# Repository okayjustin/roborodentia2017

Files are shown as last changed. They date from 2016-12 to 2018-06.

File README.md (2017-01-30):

# roborodentia2017

To rebuild the newlib libraries (embedded standard C libs):

	cd [REPOSITORY TOP LEVEL DIRECTORY]
	mkdir newlib_arm-none-eabi              					// Or whatever folder name you like
	cd newlib_arm-none-eabi
	../newlib-cygwin/configure
         --target=arm-none-eabi \
         --with-cpu=cortex-m4 \
         --with-fpu=fpv4-sp-d16 \
         --with-float=hard \
         --with-mode=thumb \
         --enable-interwork \        // Not sure if you need this one
         --enable-multilib \         // Not sure if you need this one
         --with-gnu-as \
         --with-gnu-ld \
         --disable-nls \
         --disable-newlib-supplied-syscalls  // Or whatever version of newlib source you have
    sudo make -j4 all

Then take the libc.a and libm.a from newlib_arm-none-eabi/arm-none-eabi/newlib and place them in buildTools.
Also take libnosys.a from newlib_arm-none-eabi/arm-none-eabi/thumb/libgloss/libnosys and place it in buildTools.

Then take the libc.a and libm.a from newlib_arm-none-eabi/arm-none-eabi/fpu/newlib and place them in buildTools.
Also take libnosys.a from newlib_arm-none-eabi/arm-none-eabi/fpu/libgloss/libnosys and place it in buildTools.

Debugging tips:

    > openocd -f firmware/buildTools/st_nucleo_f4.cfg
    > arm-none-eabi-gdb firmware/build/program.elf
    (gdb) target remote localhost:3333
    (gdb) monitor reset halt
    (gdb) b main.c:50
    (gdb) p data[0]
    (gdb) x/1hx 0x40005400

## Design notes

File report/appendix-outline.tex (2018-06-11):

\include{appendices/mechanical_bom}
\include{appendices/schematic}
\include{appendices/layout}
\include{appendices/pcb_bom}
\include{appendices/stm32cubemx_report}
\include{appendices/x_perf}
\include{appendices/y_perf}
\include{appendices/angle_perf}
\include{appendices/all_perf}

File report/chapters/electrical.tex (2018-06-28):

\chapter{Electrical Design}
The electronics of the robot use a combination of off-the-shelf parts and custom designed circuits. An STM32F446RE microcontroller handles low-level hardware control and interfacing such as reading sensors and supplying motor driver control signals while a Raspberry Pi 3 Model B microcomputer processes the data within the artificial neural network and determines motor speeds and directions \cite{stm32f446re}\cite{raspberrypi}. The two processors communicate through a common UART (universal asynchronous receiver-transmitter) link. The other electronic components include a battery, voltage regulation, sensors, motors, and motor drivers.

\section{Power}
A four cell, 1,800 mAH (milliamp-hour) lithium polymer (LiPo) battery powers the entire system. Polarized XT60 connectors provide mechanical reverse polarity protection. The battery voltage varies between 16.8 V when fully charged and 14.8 V when depleted so two off-the-shelf DC-DC switching regulators, shown in Figure \ref{fig:smps}, buck battery voltage down to produce 12 V and 7 V supplies. The high-efficiency switching regulators accept a 7 -- 40 V supply and can output 1.2 -- 35 V at 8 A. The 12 V bus powers the three motor drivers boards while the 7 V bus powers the STM32 Nucleo-64 development board and two AZ1085CD low-dropout linear regulators (LDO) located on the interconnect PCB. One LDO produces a 5 V bus and the other 3.3 V, each at 3 A. The LDOs possess 72 dB power supply rejection ratio, reducing the switching noise. 
\begin{figure}[H]   % [h] means here
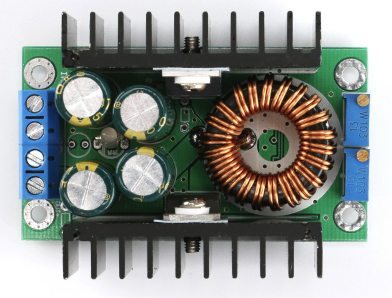
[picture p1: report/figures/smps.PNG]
	\centering 
	\caption{DC-DC Buck Regulator \cite{smps}}\label{fig:smps}
\end{figure}

\section{Sensors}
The robot uses five off-the-shelf sensors for determining its position: four VL53L0X laser rangefinders and one Adafruit 9-DOF inertial measurement unit (IMU).

\subsection{Adafruit 9-DOF IMU}
The Adafruit 9-DOF IMU incorporates the L3DG20H gyroscope and LSM303DLHC accelerometer/compass combo on a single carrier board to allow full inertial measurement in a convenient form factor \cite{adafruit_imu}. Figure \ref{fig:imu} shows the IMU mounted in the 3D printed bracket. The robot uses the accelerometer and magnetic compass to realize a tilt-compensated compass but makes no use of the gyroscope. The LSM303DLHC can measure both acceleration and magnetic fields in three dimensions with configurable bandwidth and full-scale ranges. It uses 400 kHz I\textsuperscript{2}C for control and data transfer and draws power from the 3.3 V supply. 
\begin{figure}[H]   % [h] means here
	\centering 
	\caption{Adafruit 9-DOF IMU Mounted}\label{fig:imu}
\end{figure}
Raw measurements from the IMU possess significant offset and scaling error so a calibration routine is required. The accelerometer and magnetometer calibration process uses the FreeIMU program written by Fabio Varesano \cite{freeimu}. The program features a graphical user interface (GUI), shown in Figure \ref{fig:cal_gui},  to display accelerometer and magnetometer measurements in real time and plots them in 3D space. The calibration program was originally designed to calibrate the open-source FreeIMU IMU when connected to an Arduino with the FreeIMU calibration firmware; the program's device communication back-end was specifically modified for this application to accept the LSM303DLHC IMU connected to an STM32 microcontroller with custom firmware. The calibration algorithm assumes that the sensor's measurements are linearly distorted and therefore produces a linear scaling factor and offset for each of six measurements (accelerometer X, Y, Z and magnetometer X, Y, Z). The correction algorithm is shown in Equation \ref{eq:imu_cal} where $val$ can represent any of the six measurements.
\begin{equation}
\label{eq:imu_cal}
val_{calibrated} = m_{scale} val_{measurement} + b_{offset}
\end{equation}

\begin{figure}[H]   % [h] means here
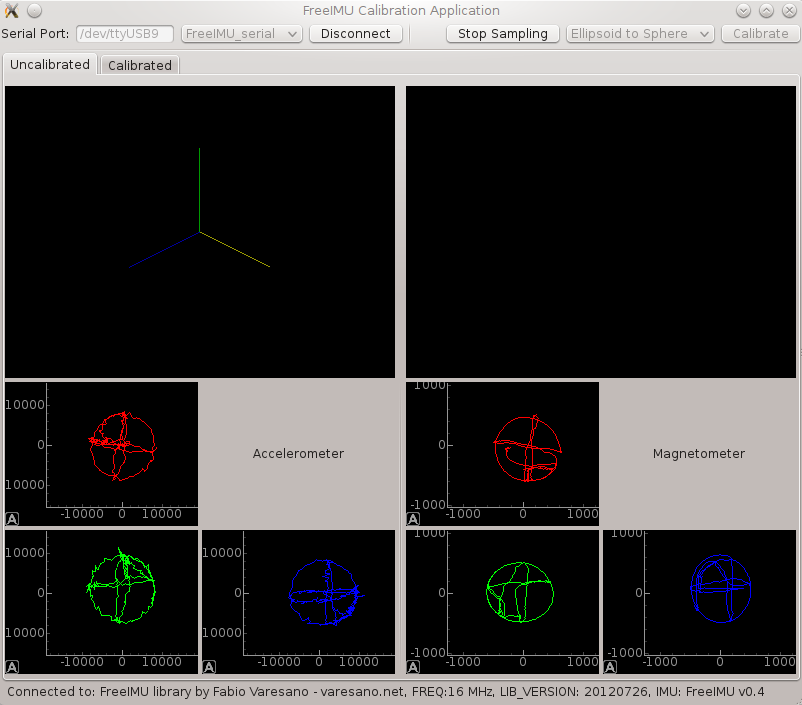
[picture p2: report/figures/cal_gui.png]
	\centering 
	\caption{FreeIMU GUI \cite{freeimu}}\label{fig:cal_gui}
\end{figure}

The calibration procedure is as follows:
\begin{enumerate}
	\item \ssp Mount IMU on fully assembled robot and connect to the microcontroller.
	\item \ssp Connect microcontroller serial port to computer through Serial-to-USB converter.
	\item \ssp Click ``Begin Sampling'' to start recording magnetometer and accelerometer measurements.
	\item \ssp Point the IMU x-axis at the ground and rotate \ang{360} around that axis. Repeat for y-axis and z-axis.
	\item \ssp Point the IMU x-axis at the sky and rotate \ang{360} around that axis. Repeat for y-axis and z-axis.
	\item \ssp Repeat Steps 3 and 4 at least twice to increase data size.
	\item \ssp Click ``Stop Sampling''.
	\item \ssp Click ``Calibrate'' to calculate scaling and offset constants.
\end{enumerate}

Since the IMU is rotated slowly, it experiences a maximum acceleration of 1 G towards the ground as well as a maximum magnetic vector whose specific magnitude and direction depends on the IMU's location on Earth. The procedure ensures that ends of each IMU axis (+X, -X, +Y, -Y, +Z, -Z) eventually receive the maximum acceleration and magnetic field \cite{tedaldi_pretto_menegatti_2014}. To ensure hard-iron errors (such as from motors and permanent magnets) as well as soft iron errors (from local ferromagnetic materials like steel) are compensated for in the calibration, the process should be performed with the fully assembled robot and redone each time the robot is modified \cite{hard_soft_correction}. Since the expected fields are known (acceleration due to gravity, strength of Earth's magnetic field), the required linear transformation can be calculated \cite{freeimu}. Details of the exact algorithm can be found at the FreeIMU website.

\subsection{VL53L0X Rangefinders}
The rangefinders, marketed by STMicroelectronics as the ``world's smallest Time-of-Flight ranging sensor'', are capable of measuring between 30 and 2000 mm with a 30 Hz sample rate \cite{vl53l0x}. They operate by firing pulsed light from a vertical cavity surface emitting laser (VCSEL), measuring time taken for the laser pulse to reflect back, and calculating the distance based on the known speed of light. The robot uses cheap \$8 VL53L0X breakout boards in lieu of designing and assembling custom carriers; the sensor itself comes in a 4.4 x 2.4 mm lead-less package making hand soldering prohibitively difficult. Figure \ref{fig:rangefinder} shows the sensor board mounted in the 3D printed bracket. The sensor breakout boards include the VL53L0X module, decoupling capacitors, an LDO for the sensor's 2.8 V power supply, and level shifters for the I\textsuperscript{2}C lines. Control and data transfer both occur over 400 kHz I\textsuperscript{2}C so the breakout only requires four wires: 3.3 V, ground, and the I\textsuperscript{2}C data and clock lines. To characterize the accuracy and precision of the sensor, distance measurements were taken by targeting the sensor at a sheet of standard white printer paper. The data is compared with measurements from a tape measure; results are shown in Figure \ref{fig:rangefinder_measurement}. 
\begin{figure}[H]   % [h] means here
	\centering 
	\caption{VL53L0X Rangefinder Mounted}\label{fig:rangefinder}
\end{figure}
\begin{figure}[H]   % [h] means here
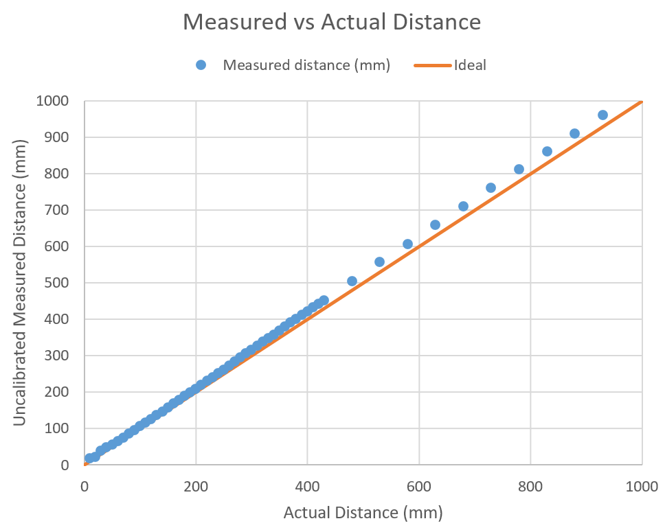
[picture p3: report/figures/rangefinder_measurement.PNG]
	\centering 
	\caption{VL53L0X Measured vs. Actual Distance}\label{fig:rangefinder_measurement}
\end{figure}
Since the measurements primarily appear to possess linear error, only a linear correction is required as in Equation \ref{eq:rf_cal}:
\begin{equation}
\label{eq:rf_cal}
	d_{calibrated} = m_{scale} d_{measurement} + b_{offset}
\end{equation}
$d_{measurement} $ is distance as returned by the sensor, $m_{scale} = 0.96502507$, $b_{offset} = -3.8534743$, and $d_{calibrated}$ is the calibrated distance. The squared error for each data point before and after calibration is shown in Figure \ref{fig:rangefinder_calibrated}. The total squared error for the uncalibrated and calibrated data points are 342.3 mm and 15.0 mm, respectively, indicating the successful use of an appropriate model and constants.
\begin{figure}[H]   % [h] means here
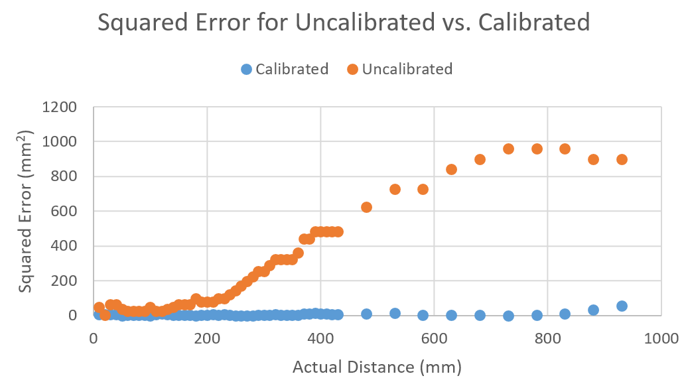
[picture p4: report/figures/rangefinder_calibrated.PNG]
	\centering 
	\caption{VL53L0X Squared Error for Uncalibrated vs. Calibrated}\label{fig:rangefinder_calibrated}
\end{figure}
Additionally, 100 measurements were taken at each distance and the variance computed to characterize the measurement spread. The results are shown in Figure \ref{fig:rangefinder_stddev}. The rangefinders are very accurate; at 900 mm with calibration, the error is only 7 mm or 0.8\% error. Of course, this error is with respect to the average measurement at 900 mm. At 900 mm, the standard deviation is 14 mm so individual measurements can vary, especially with non-ideal surfaces. The closer the target, the more accurate and less varied the measurement. No experiments were carried out to determine the measurement characteristics on various colored, textured, transparent, or angled surfaces as the expected target surface is white painted wood.
\begin{figure}[H]   % [h] means here
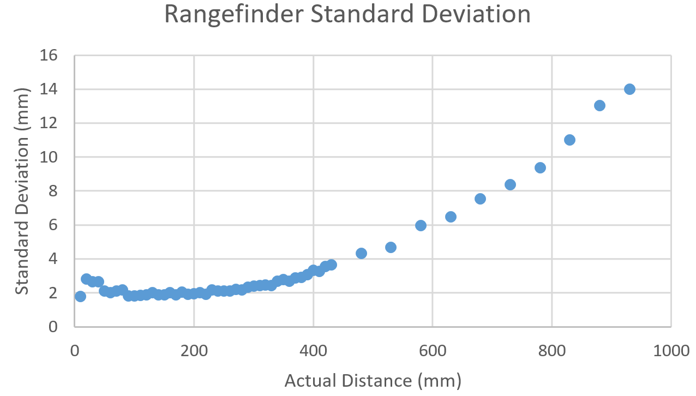
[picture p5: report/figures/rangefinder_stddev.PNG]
	\centering 
	\caption{VL53L0X Standard Deviation}\label{fig:rangefinder_stddev}
\end{figure}
\section{Motors}
The robot uses four 12V Pololu 37D 70:1 geared motors to drive the wheels. The motors draw about 630 mA each at full speed steady state of 234 rpm (24.46 rad/s) and have a maximum acceleration of 4,100 rpm/s (430 rad/s\textsuperscript{2}). These values vary slightly from motor to motor due to slight differences in manufacturing and load. Each wheel experiences slightly different static normal force since the robot's weight is not evenly distributed across the four wheels. Additionally, the dynamic load varies because the ground and base platform are not perfectly flat as well as the minor effects from the robot's weight shifting due to acceleration. The motors come with quadrature rotary encoders which were used in motor characterization but not in the robot itself.

\section{Motor Drivers}
The system uses three off-the-shelf L298N motor driver boards since they are easily obtainable for less than \$6 each and incorporate features such as heat-sinking, flyback voltage protection, supply filtering, and screw terminal connections \cite{l298n_digi}. Implementing comparable motor drivers with a similar feature set would undoubtedly cost more both monetarily and in design effort. The L298N dual H-bridge driver can supply 2\,A maximum output per bridge using a 5 -- 35 V supply. Two motor drivers handle the four robot drive motors while the third powers the blower fan and shooting mechanism motors. 

Figure \ref{fig:l298n} shows a wiring diagram for each motor driver. The board uses four digital control inputs, each controlling the state of one half-bridge. Each motor uses a pair of inputs: IN1 and IN2 control one motor while IN3 and IN4 control the other. To achieve direction and speed control, IN1 and IN3 are pulse width modulated (PWM) while IN2 and IN4 are digitally set. Table \ref{tab:L298N_truth_table} is a truth table of the motor state versus inputs.
\begin{figure}[H]   % [h] means here
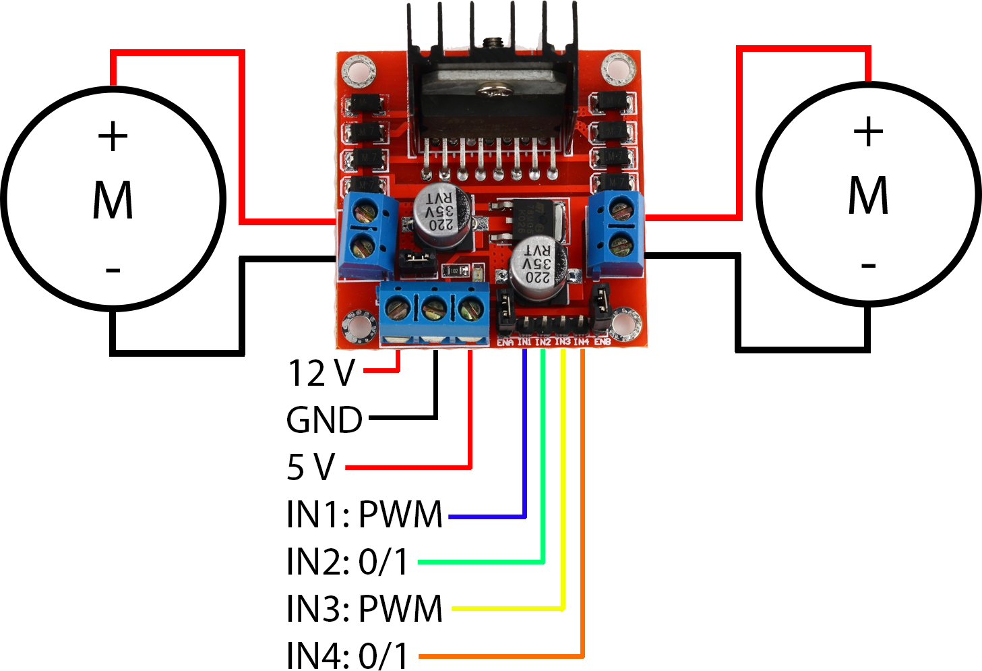
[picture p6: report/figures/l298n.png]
	\centering 
	\caption{L298N Motor Driver Wiring Diagram \cite{l298n}}\label{fig:l298n}
\end{figure}
\begin{table}[h]
	\centering \caption{Motor Control Truth Table}	\label{tab:L298N_truth_table}
	\begin{tabular}{ccc}
		\toprule 
		IN1/IN3 Duty Cycle & IN2/IN4 State & Motor State \\ 
		\midrule 
		0\% & 0 & Stopped \\ 
		\textgreater 0\% & 0 & Forward, speed increases with duty cycle \\ 
		\textless 100\% & 1 & Reverse, speed decreases with duty cycle \\ 
		100\% & 1 & Stopped \\ 
		\bottomrule
	\end{tabular} 
\end{table}

\section{Servo}
A GWS S03N standard servo powered from the 5 V bus actuates the gating mechanism in the ball hopper. Most servos are controlled by driving the control wire with a pulse width modulated (PWM) signal with a period of 15 -- 25 ms and a pulse width between 0.5 ms and 2.5 ms where the pulse width determines the position of the servo as shown in Figure \ref{fig:servo_pulse_width}. 
\begin{figure}[H]   % [h] means here
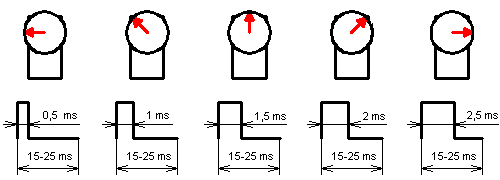
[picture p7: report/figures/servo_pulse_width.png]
	\centering 
	\caption{Servo PWM Control Scheme \cite{servo_pulse_width}}\label{fig:servo_pulse_width}
\end{figure}
Due to loose tolerances, the actual required pulse widths can vary from servo to servo, requiring calibration to obtain accurate positional control. The process for calibration is simple: apply various pulse widths and record the resulting servo positions. The calibrated pulse widths and servo angles are recorded in Table \ref{tab:servo_angles}. Clearly, the actual required timings for specific angles possess significant deviations from nominal. 
\begin{table}[h]
	\centering \caption{Servo Required Pulse Widths}	\label{tab:servo_angles}
	\begin{tabular}{cc}
		\toprule 
		Servo Position & Pulse Width (ms) \\ 
		\midrule 
		\ang{0} & 0.674 \\ 
		\ang{45} & 1.082 \\
		\ang{90} & 1.490 \\ 
		\ang{135} & 1.898 \\ 
		\ang{180} & 2.306 \\ 
		\bottomrule 
	\end{tabular} 
\end{table}

\section{Microcontroller}
An STMicroelectronics STM32F446RE microcontroller (MCU) serves as the bridge between the robot's low-level electronics and the high-level control system running on a desktop computer. Specifically, the MCU collects data from sensors over I\textsuperscript{2}C and general purpose input/output (GPIO), generates control signals for the motor drivers and servo, and services commands from UART. The MCU resides on an STMicroelectronics Nucleo-64 development board, shown in Figure \ref{fig:nucleo64}, which conveniently integrates an ST-LINK V2 debugger, programmer, and USB-to-UART interface. The MCU uses an ARM Cortex-M4 RISC (reduced instruction set computer) core running at 180 MHz with hardware FPU (floating point unit) and adaptive real-time accelerator. It provides numerous communication interfaces, timers, and GPIO as well as DMA (direct memory access) capability. The development board itself plugs into a board-to-board receptacle located at the bottom of the interconnect PCB.
\begin{figure}[H]   % [h] means here
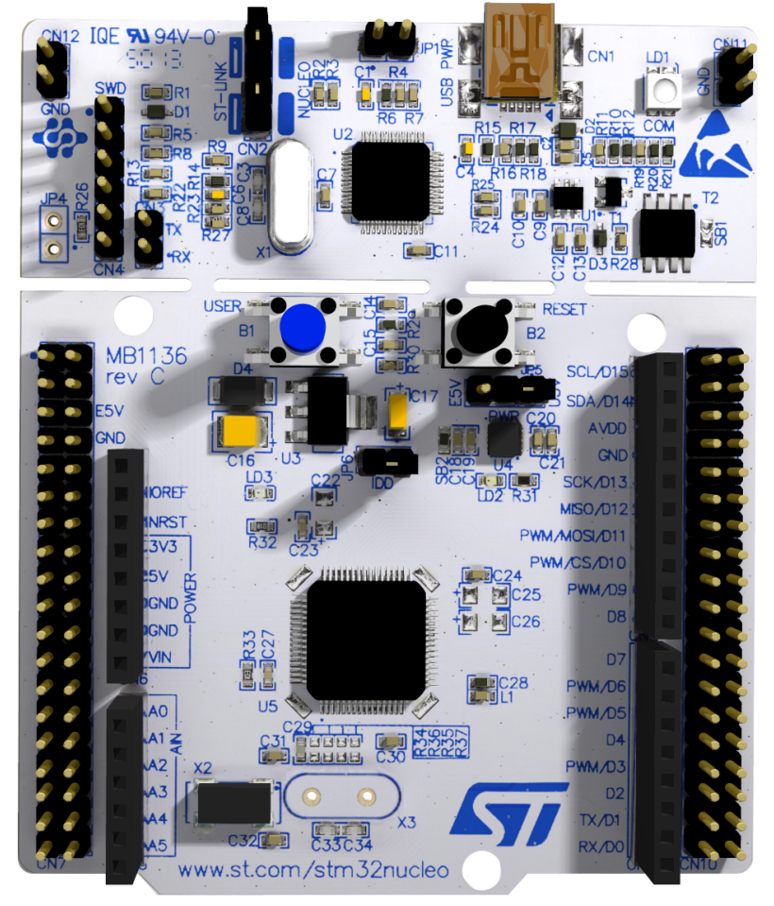
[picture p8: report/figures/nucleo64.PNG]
	\centering 
	\caption{STM32 Nucleo-64 Development Board \cite{nucleo64_manual}}\label{fig:nucleo64}
\end{figure}

\section{Interconnect PCB}
The interconnect PCB is a custom designed board with three goals: regulate voltage, route power, and connect peripherals to the development board. The PCB routes input battery power to two external buck regulators, producing 12 V and 7 V. The 7 V bus is further regulated to 5 V and 3.3 V logic rails using two AZ1085CD LDOs and then routed to the development board, sensors, etc. Most importantly, the interconnect board provides dedicated 2.0 mm JST connectors for all sensors, motor drivers, and the servo to simplify and robustify wiring across the robot. In addition, hand-crimped cables made with JST connectors and 28 gauge ribbon cable prevent disorganized point-to-point wiring. A block diagram is shown in Figure \ref{fig:interconnect_block}. The board incorporates support for additional sensors to address uncertainty in the robot's final design. Table \ref{tab:interconnect_features} lists the supported features as well as those used in the final design. 
\begin{figure}[H]   % [h] means here
	\centering 
	\caption{Electronics Block Diagram}\label{fig:interconnect_block}
\end{figure}
\begin{table}[h]
	\centering	\caption{Interconnect PCB -- Supported Features}	\label{tab:interconnect_features}
	\begin{tabular}{ccl}
		\toprule 
		Qty Available & Qty Used & \multicolumn{1}{c}{Feature} \\ 
		\midrule 
		6 & 4 & VL53L0X laser rangefinder \\ 
		1 & 1 & Adafruit 9-DOF IMU \\ 
		3 & 3 & Dual H-bridge motor driver \\
		2 & 1 & 5 V Standard servo \\ 
		2 & 0 & Infrared proximity array \\
		4 & 0 & Microswitch \\ 
		4 & 2 & Debug LED \\ 
		1 & 1 & Debug button \\
		1 & 1 & Reset button \\ 
		\bottomrule
	\end{tabular} 
\end{table}
Due to limited MCU GPIO availability, the board incorporates three TCA9554ADWR I\textsuperscript{2}C 8-bit GPIO expanders to handle low-speed signals \cite{TCA9554ADWR}. However, either through an indeterminate design error, defective ICs, or poor soldering, none of the ICs would respond to I\textsuperscript{2}C traffic so they were not used in the final design. The GPIOs meant for the microswitches were repurposed to drive some signals instead.

The system uses two 400 kHz I\textsuperscript{2}C buses to improve communication bandwidth with the numerous I\textsuperscript{2}C devices. Table \ref{tab:i2c_table} lists I\textsuperscript{2}C device addresses and bus allocation. The two buses are named I2C2 and I2C3 to maintain parity with the microcontroller's naming convention.
\begin{table}[h]
	\centering	\caption{Interconnect PCB -- I\textsuperscript{2}C Devices}  \label{tab:i2c_table}
	\begin{tabular}{clc}
		\toprule 
		\multicolumn{1}{c}{I\textsuperscript{2}C Bus} & \multicolumn{1}{c}{Device} & Address (7-bit) \\ 
		\midrule 
		I2C2 & Rangefinder 4 & 0x52 \\  
		I2C2 & Rangefinder 5 & 0x53 \\  
		I2C2 & Rangefinder 6 & 0x54 \\  
		I2C2 & Adafruit 9-DOF IMU Gyroscope & 0x69 \\ 
		I2C2 & Adafruit 9-DOF IMU Accelerometer & 0x19\\ 		
		I2C2 & Adafruit 9-DOF IMU Magnetometer & 0x1E \\ 		
		I2C2 & GPIO Expander 3 & 0x3A \\ 				
		\hline
		I2C3 & Rangefinder 4 & 0x52 \\  
		I2C3 & Rangefinder 5 & 0x53 \\  
		I2C3 & Rangefinder 6 & 0x54 \\  
		I2C3 & GPIO Expander 1 & 0x38 \\ 				
		I2C3 & GPIO Expander 2 & 0x39 \\ 
		\bottomrule				
	\end{tabular} 
\end{table}
The schematic capture and board layout were created in CadSoft EAGLE 7.4 due to its simplicity of use, popularity, and community support \cite{eagle}. The schematic can be found in Appendix \ref{appendix:schematic}, layout in Appendix \ref{appendix:layout}, and bill of materials in Appendix  \ref{appendix:pcb_bom}. The board uses two 1-ounce copper layers for cost effectiveness. Two large headers underneath the board connect to the headers on the top of the microcontroller development board while the JST connectors are placed across the top of the PCB. 18-gauge wires soldered to large plated through-holes at the right edge of the board connect the external buck regulators. All components are placed on the top side of the board (except for the development board connectors) to make hand-soldering easier. The bare PCBs, fabricated by PCBWay.com, cost \$23 for 10 copies \cite{pcbway}. The completed electronics assembly is shown in Figure \ref{fig:full_electronics}.
\begin{figure}[h]   % [h] means here
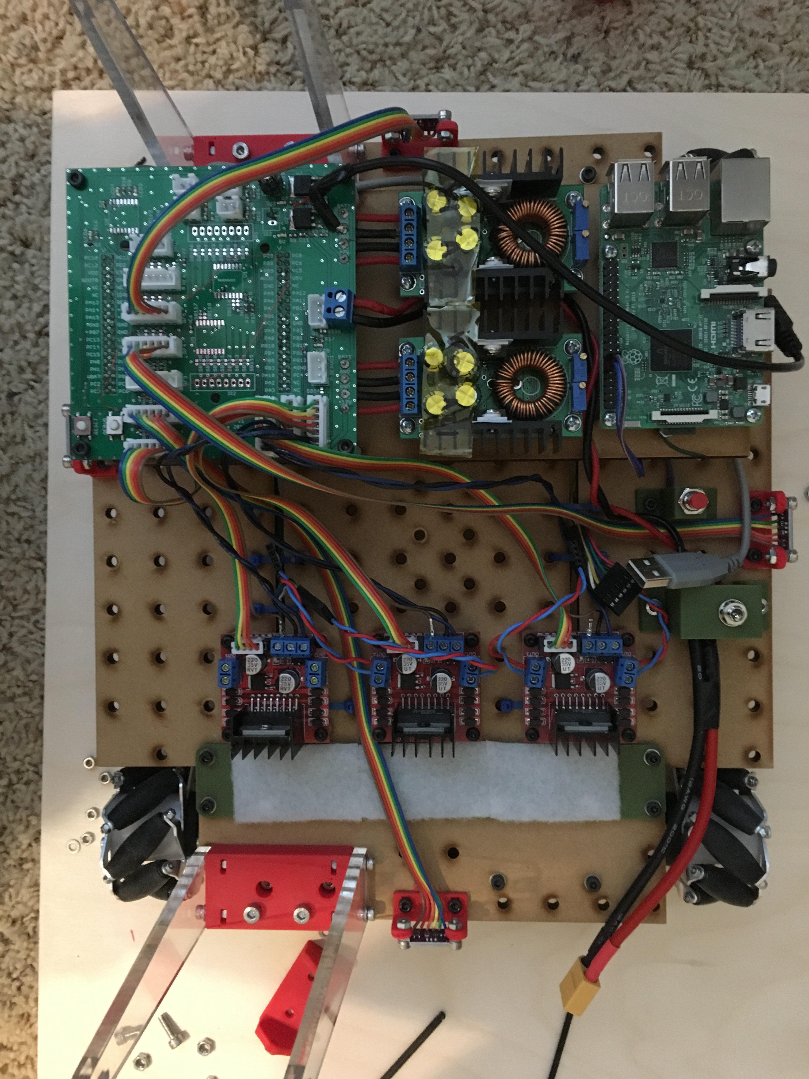
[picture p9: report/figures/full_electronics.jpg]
	\centering 
	\caption{Fully Assembled Electronics}\label{fig:full_electronics}
\end{figure}

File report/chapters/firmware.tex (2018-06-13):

\chapter{Firmware Design}
\section{STM32CubeMX}
The robot uses an STMicroelectronics STM32F446RE microcontroller (MCU) for low level sensor interfacing and motor control signal generation. The MCU sends filtered sensor data to a Raspberry Pi \cite{raspberrypi} and receives speed and direction commands for each motor. Before starting the electrical design, the various hardware signals must be assigned to the MCU's GPIO with consideration for the device's peripherals such as timers and I\textsuperscript{2}C buses, a process aided by STMicroelectronics' configuration program, STM32CubeMX, shown in Figure \ref{fig:stm32cubemx} \cite{stm32cubemx}. Within the program, the user selects which MCU to configure and a graphical representation of the chip is shown in the GUI. The MCU's GPIO pins are arranged into banks of up to 16 pins each called ports. For example, PC2 is the second pin in Port C while PB11 is Pin 11 in Port B. The left column of the GUI lists the device peripherals including analog-to-digital converters (ADCs); various buses such as SPI, USART, and USB; and timers. Peripheral settings can be chosen here such as USART mode (asynchronous, single-wire, LIN, etc) and flow control as well as timer clock sourcing and channel modes.
\begin{figure}[H]   % [h] means here
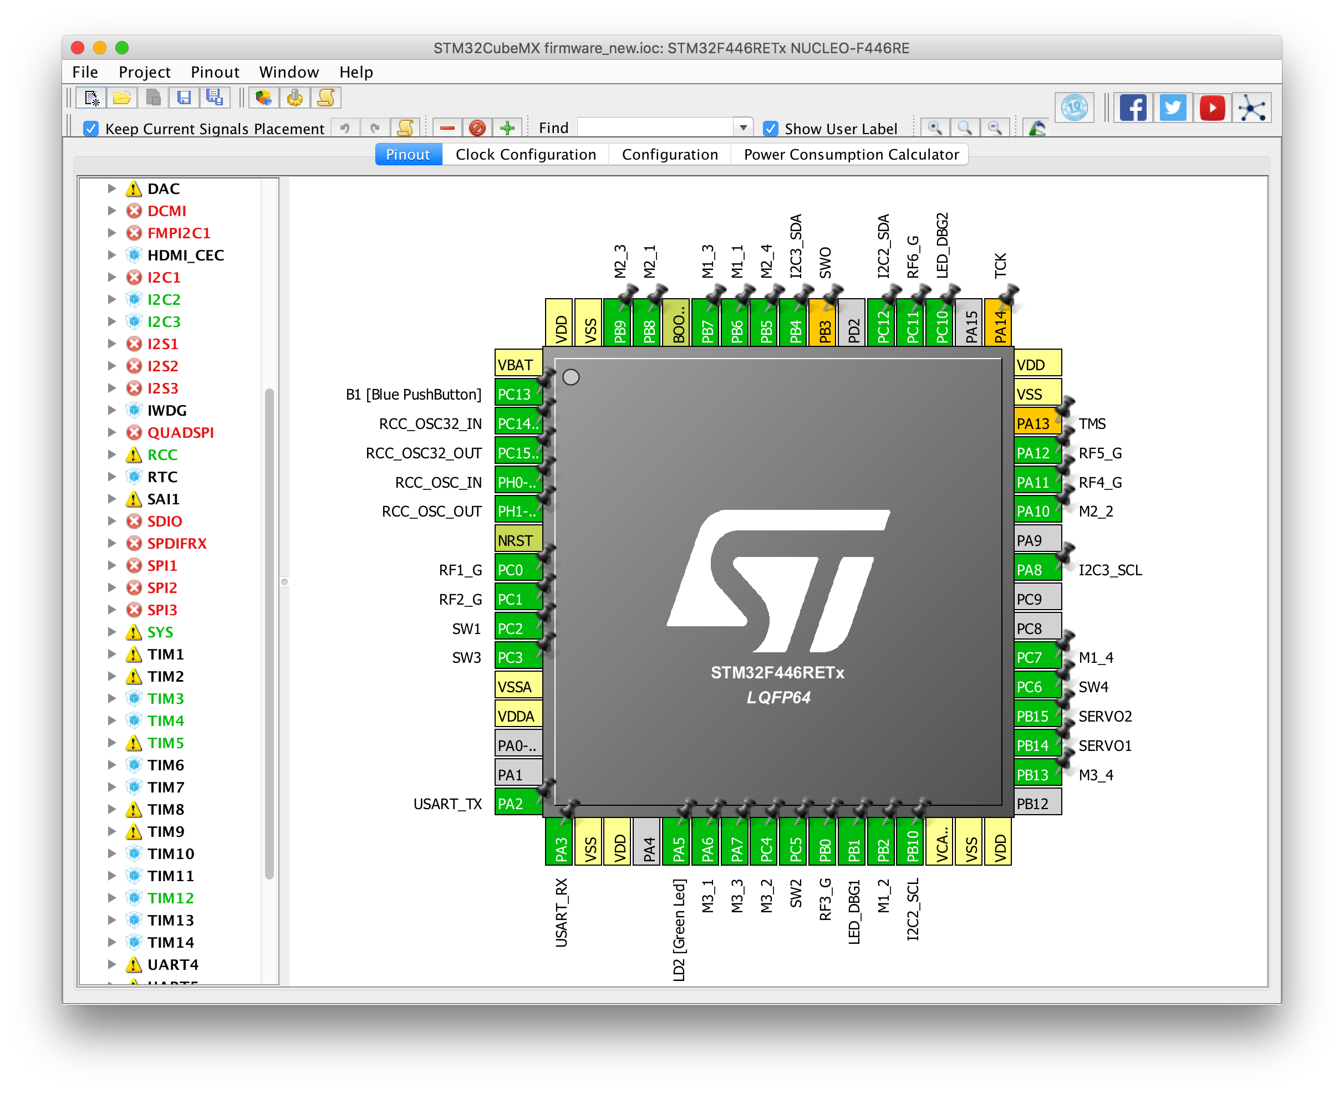
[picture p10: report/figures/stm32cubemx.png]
	\centering 
	\caption{STM32CubeMX}\label{fig:stm32cubemx}
\end{figure}
The program greatly reduces development effort. Clicking a pin on the GUI brings up a menu of possible assignments. For example, clicking PB15, seen in Figure \ref{fig:stm32cubemx_pin}, shows that the pin can be used for the ADC, I2S2, as SPI2's MOSI, TIMER12's CH2 output, part of the USB differential data pair, as standard GPIO input or output, and more. As pins are assigned to various purposes, the program continually checks for compatibility issues and pin conflicts so a user can iteratively assign pins until all errors clear. For example, using a particular set of timers may actually prevent the use of I2C1 so either I2C2 or I2C3 must be used instead. This process is much faster and less error-prone than searching through the MCU's immense datasheet to manually check for assignment conflicts within every peripheral.
\begin{figure}[H]   % [h] means here
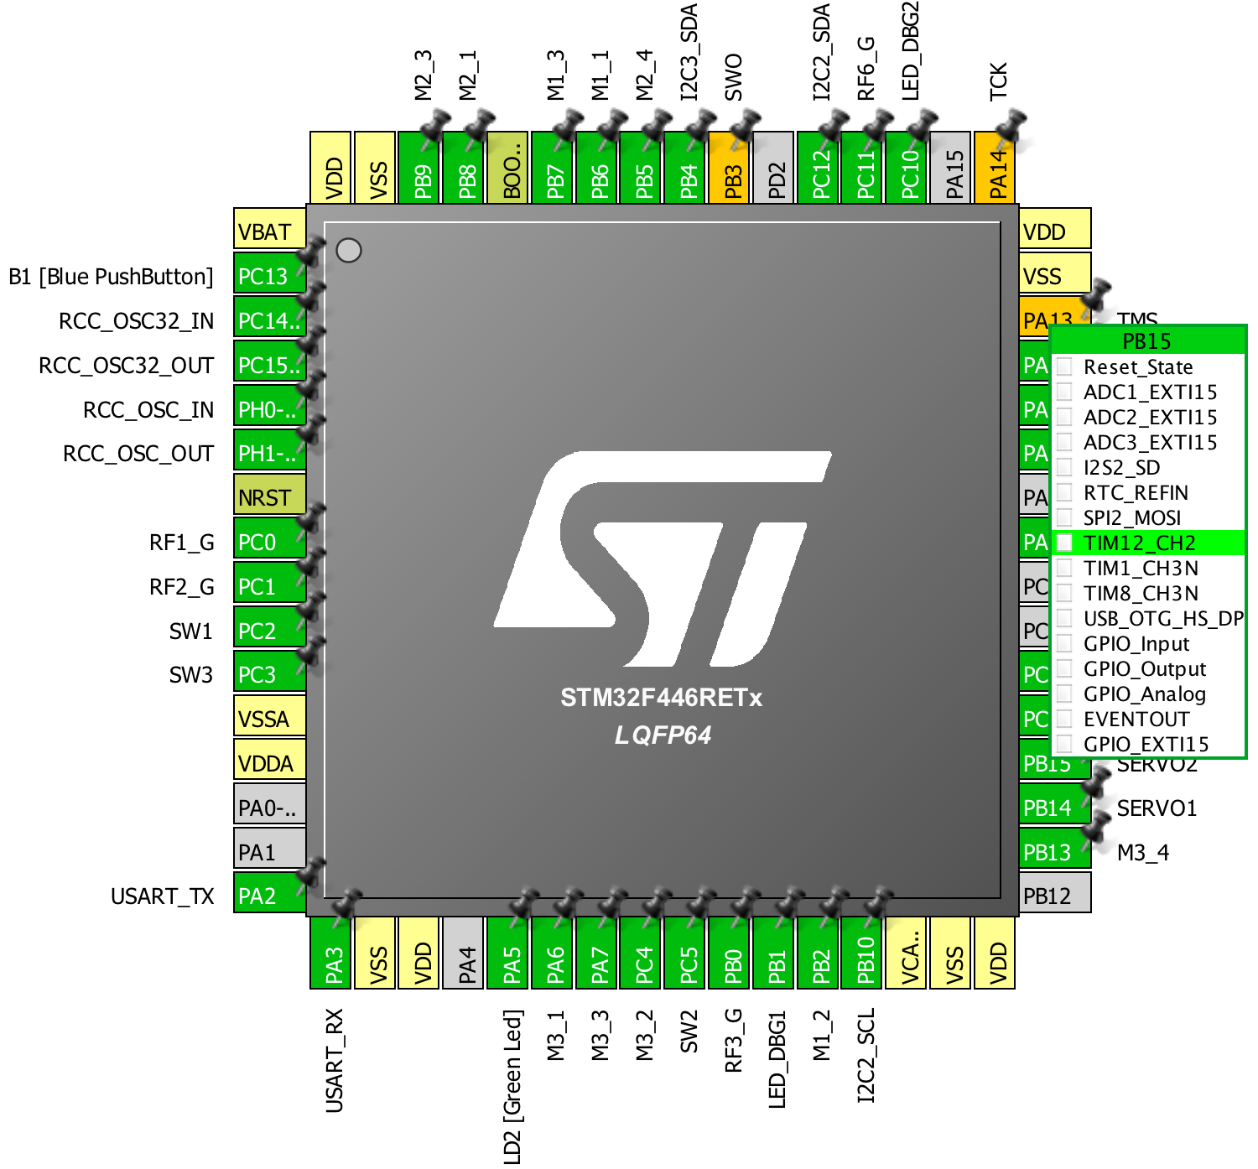
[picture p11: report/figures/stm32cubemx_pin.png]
	\centering 
	\caption{STM32CubeMX -- Pin Menu}\label{fig:stm32cubemx_pin}
\end{figure}
The software also provides device-wide clock and PLL configuration as shown in Figure \ref{fig:stm32cubemx_clocks}. The MCU uses an external 8 MHz crystal to drive the internal PLL which then generates a 180 MHz system clock. Since the system is optimized for performance instead of power-saving, the advanced peripheral bus (APB) clocks run at 45 MHz and 90 MHz for APB1 and APB2, respectively \cite{stm32f446re}. 
\begin{figure}[H]   % [h] means here
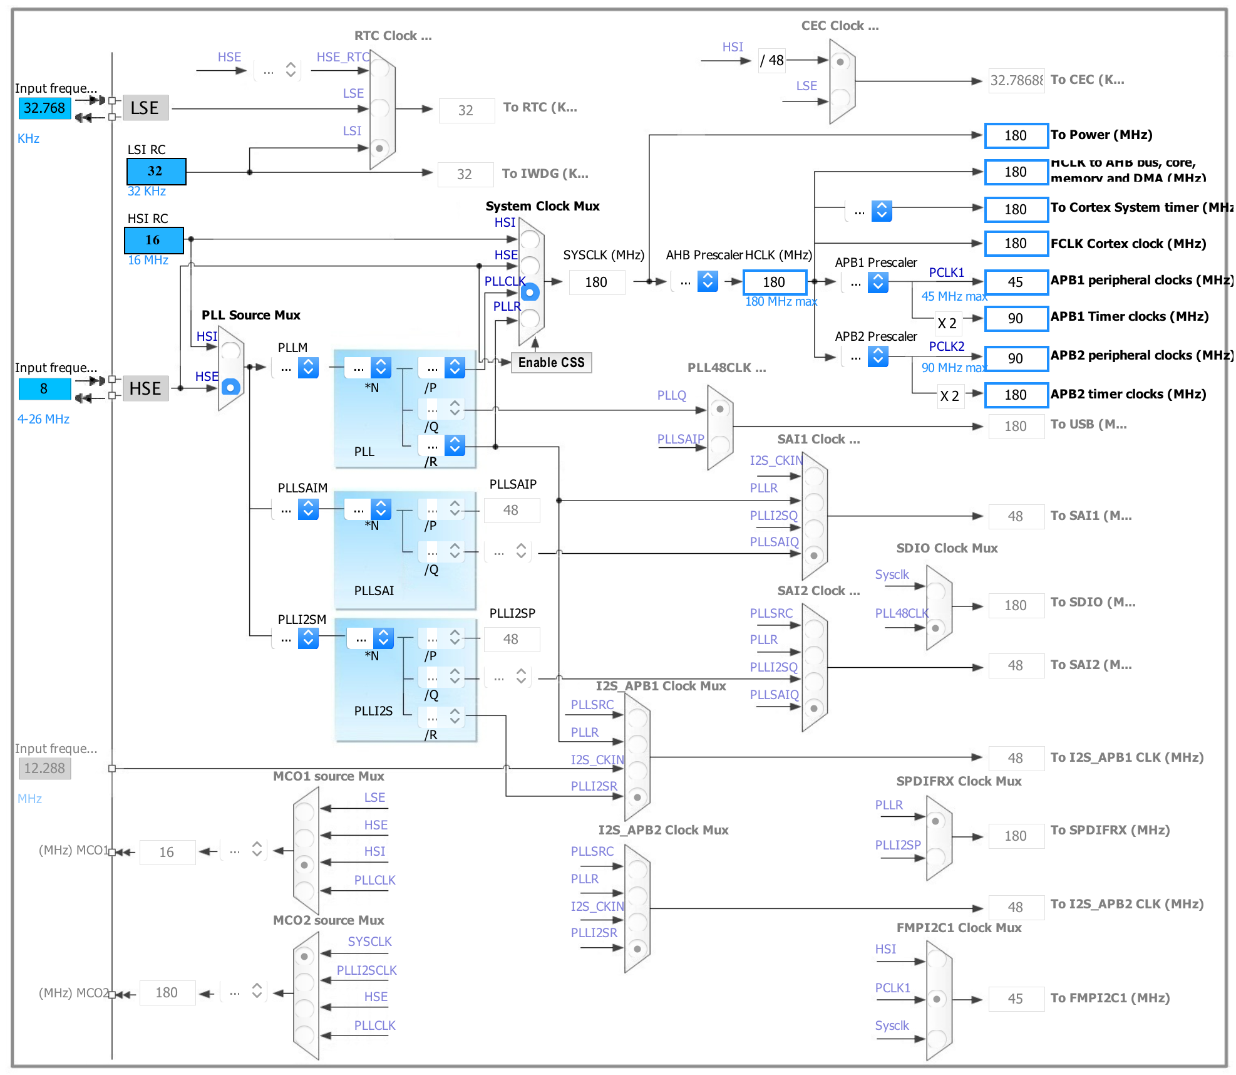
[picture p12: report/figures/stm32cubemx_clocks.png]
	\centering 
	\caption{STM32CubeMX -- Clock Configurator}\label{fig:stm32cubemx_clocks}
\end{figure}
Another tab within STM32CubeMX provides detailed peripheral configuration, shown in Figure \ref{fig:stm32cubemx_config}. Both I\textsuperscript{2}C buses are set to 400 kHz with a 2:1 T\textsubscript{low}:T\textsubscript{high} duty cycle to meet the minimum pulse width requirement of slave devices. The USART peripheral is configured to 921,600 bits/s, 8-bit words, no parity, and one stop bit. The direct memory access (DMA) controller is set to process requests from the I\textsuperscript{2}C and UART peripherals to reduce processor load. 
\begin{figure}[H]   % [h] means here
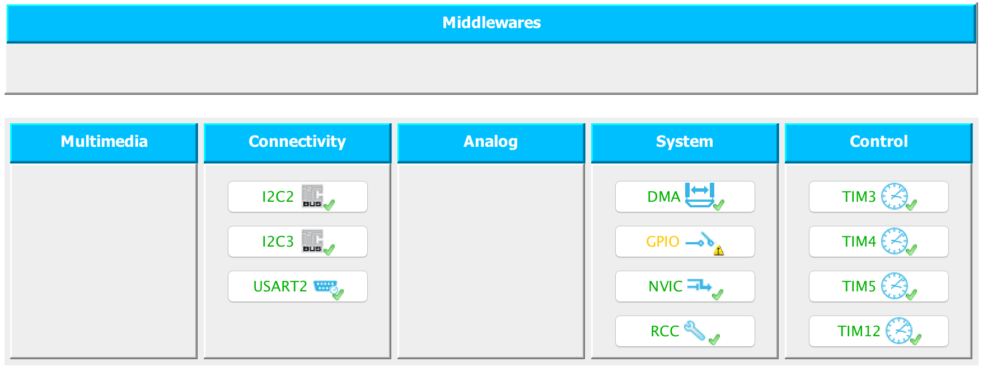
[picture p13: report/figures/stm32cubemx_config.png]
	\centering 
	\caption{STM32CubeMX -- Peripheral Configurator}\label{fig:stm32cubemx_config}
\end{figure}
The robot uses four of the MCU's timers: TIMER3, TIMER4, TIMER5, and TIMER12. Each of these timers sources its base clock from the APB1 clock which is 90 MHz. TIMER3 and TIMER4 output 6 PWM control signals for the motor drivers. They are set to count upward and reset after the counter reaches 2047 to produce a 43.9 kHz PWM frequency in the ultrasonic range. TIMER5, used for delay and timing functions, employs a clock prescaler of 9000 so the counter increases every 0.1 ms and never resets; the 32-bit counter has a maximum value of 4,294,967,295 corresponding to a counter rollover period of about 5 days. Finally, TIMER12 drives the PWM signals for servo control. It uses a 45 prescaler and a 50,000 counter period to produce a 40 Hz PWM frequency.

After configuring the various items above, STM32CubeMX can generate common boilerplate plate code to initialize and configure all the devices. Include and source files are generated on a by-peripheral basis to compartmentalize code. The program also generates a report of the device configuration, attached in Appendix \ref{appendix:stm32cubemx_report}.

\section{Microcontroller Firmware}
The firmware, written in C and compiled with gcc, consists of a main file in conjunction with peripheral driver files \cite{gcc}. The dependency graph is shown in Figure \ref{fig:firmware_dependencies} with file descriptions shown in Table \ref{tab:firmware_file_desc}.  STM32CubeMX automatically generated several files to which user code was added for specific robot functions. The VL53L0X API, provided by STMicroelectronics, was also modified for the STM32F446 platform. Table \ref{tab:firmware_specs} lists the firmware requirements.
\begin{figure}[H]   % [h] means here
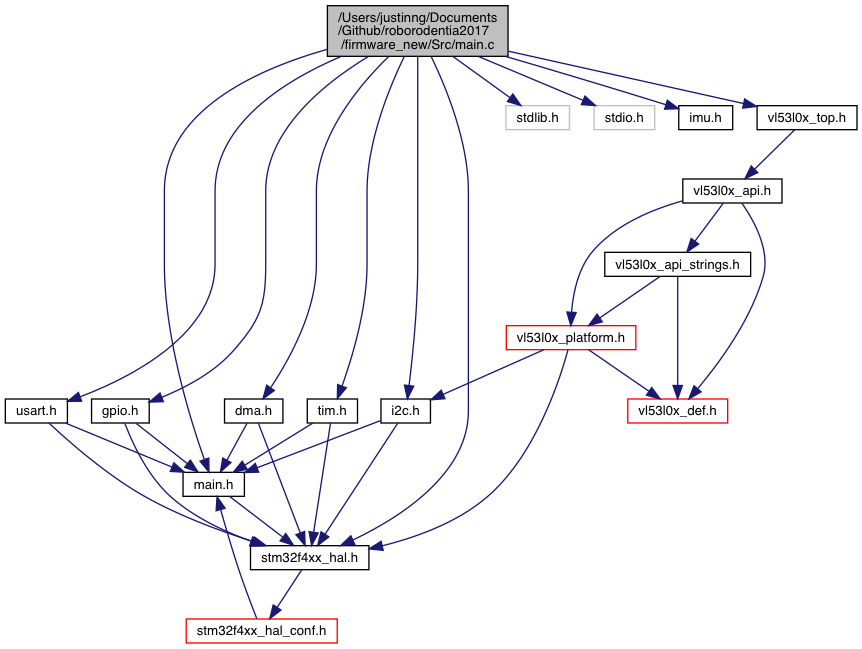
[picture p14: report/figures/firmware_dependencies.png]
	\centering 
	\caption{Firmware Dependency Graph for main.c}\label{fig:firmware_dependencies}
\end{figure}
\begin{table}[H]
	\centering	\caption{Firmware -- Source File Summary} 	\label{tab:firmware_file_desc}
	\begin{tabular}{r|l}
		\toprule 
		\multicolumn{1}{c}{File (.h/.c)} & \multicolumn{1}{c}{Description} \\ 
		\midrule 
		main & Initialization and main loop. \\  
		stm32f4xx\_hal & Hardware abstraction layer driver. \\  			
		dma & Sets up DMA priorities and enables DMA interrupts. \\  		
		i2c & Initializes I\textsuperscript{2}C buses, read/write, finds active devices. \\  		
		tim & Initializes timers 3, 4, 5, and 12. \\  		
		usart & Initializes UART, functions to write to bus, DMA callbacks. \\  		
		gpio & Configures GPIO modes (in/out), speeds, and pull-ups/pull-downs. \\  		
		vl53l0x\_top & STMicroelectronics API for configuring and reading rangefinders. \\  				 
		imu & Initializes IMU; read gyroscope, accelerometer, and magnetometer. \\ 
		\bottomrule 		
	\end{tabular} 
\end{table}
\begin{table}[H]
	\centering	\caption{Firmware -- Requirements} 	\label{tab:firmware_specs}
	\begin{tabular}{c|l}
		\toprule 
		 & \multicolumn{1}{c}{Requirements} \\ 
		 \midrule 
		1. & Initialize I\textsuperscript{2}C sensors including rangefinders and IMU. \\  
		2. & Read and store data from sensors. \\  
		3. & Filter data from sensors to reduce noise. \\  
		4. & Generate PWM signal to drive servo. \\  
		5. & Generate control signals to motor drivers. \\  
		6. & Sequence launcher motors, blower fan, and servo to fire balls. \\  
		7. & Flash LED to indicate error state. \\  
		8. & Communicate with computer over UART link. Add'l specifications in \ref{tab:firmware_uart_specs}. \\ \bottomrule 
	\end{tabular} 
\end{table}

\subsection{UART Commands}
The MCU responds to UART commands from a computer. The command syntax generally involves a sequence of one or more 8-bit characters. Table \ref{tab:firmware_uart_specs} lists the available commands. 
\begin{table}
	\centering	\caption{Firmware -- UART Commands}  \label{tab:firmware_uart_specs}
	\begin{tabularx}{\textwidth}{@{} c|Y @{}}
		\toprule 
		Syntax & \multicolumn{1}{c}{Command} \\ 
		\midrule 
		A & Start reading all rangefinders. \\  
		B & Returns sensor data in binary form (machine-readable). \\  
		D & Return sensor data in text form (human-readable). \\  
		I\textless BUS\textgreater & Scans I\textsuperscript{2}C bus and returns addresses of active devices. \\ 
		& \textless BUS\textgreater\ valid values: \\ 
		& \qquad 2 : Scan I2C2. \\
		& \qquad 3 : Scan I2C3. \\  \addlinespace
		L\textless SIDE\textgreater & Launch balls from one side of the hopper. \\
		& \textless SIDE\textgreater\ valid values: \\ 
		& \qquad L : Launch balls from left side. \\
		& \qquad R : Launch balls from right side. \\
		& \qquad S : Stop all motors. \\  \addlinespace
		M\textless FL\textgreater\textless BL\textgreater\textless BR\textgreater\textless FR\textgreater & Sets motor duty cycle calculated as \textless arg\textgreater\ divided by 2047. Each argument accepts a integer from 0 to 2047. \\
		& \textless FL\textgreater\ : PWM value for front left motor. \\
		& \textless BL\textgreater\ : PWM value for back left motor. \\
		& \textless BR\textgreater\ : PWM value for back right motor. \\
		& \textless FR\textgreater\ : PWM value for front right motor. \\  \addlinespace	
		V & Returns firmware version info. \\  
		Z & Return debug button pressed flag. \\ 
		\bottomrule 
	\end{tabularx} 
\end{table}

\subsubsection{UART Receiving}
After receiving a character on the UART bus, the DMA places it into \cinline{rxBuffer} and fires an interrupt. The MCU enters the UART receive complete DMA callback, shown in Listing \ref{list:uart_receive}, which collects the received characters into a command string stored in \cinline{stringBuffer}. If the UART receives a new line or line return character, the callback appends a null character to the string and calls \cinline{consoleCommand()} to parse and execute the command. The define \cinline{UART_RX_WRITEBACK} controls whether received characters and commands are echoed.
\begin{clisting}[caption={UART Receive Callback},label={list:uart_receive}]
#define RX_BUFFER_MAX_LENGTH 32 
#define UART_RX_WRITEBACK 0

uint8_t rxBuffer = '\000';
uint8_t stringBuffer[RX_BUFFER_MAX_LENGTH];
uint8_t stringBufferIndex;

void HAL_UART_RxCpltCallback(UART_HandleTypeDef *huart)
{
    uint8_t i;

    // Clear buffer
    if (stringBufferIndex == 0) {for (i = 0; i < RX_BUFFER_MAX_LENGTH; i++) stringBuffer[i] = 0;}	

    if ((rxBuffer != 10) && (rxBuffer != 13))	//if received data different from ascii 13 (enter)
    {
        if (stringBufferIndex < RX_BUFFER_MAX_LENGTH){
            stringBuffer[stringBufferIndex++] = rxBuffer; //add data to stringBuffer
        }
    }
    else // If received data = 10 or 13
    {
        if (stringBufferIndex < RX_BUFFER_MAX_LENGTH){
            stringBuffer[stringBufferIndex++] = '\0'; //add null char
        } else {
            stringBuffer[RX_BUFFER_MAX_LENGTH] = '\0'; //add null char
        }

        if (UART_RX_WRITEBACK){
            HAL_UART_Transmit(&huart2, (uint8_t *)&stringBuffer, stringBufferIndex, 0xFFFF);
            printf("\r\n");
        }
        consoleCommand((uint8_t *)&stringBuffer, stringBufferIndex);
        stringBufferIndex = 0;
    }

    if (UART_RX_WRITEBACK){
        HAL_UART_Transmit(&huart2, (uint8_t *)&rxBuffer, 1, 1);
    }
}
\end{clisting}

\subsubsection{UART Transmitting}
The \cinline{\_write()} function is overridden to redirect \cinline{printf()} output to UART using the code in Listing \ref{list:redirect_printf}.
\begin{clisting}[caption={Redirect printf()},label={list:redirect_printf}]
// Redirect printf to UART
int _write (int fd, char *ptr, int len) 
{ 
	transmitUART(ptr, len);
	return len; 
}
\end{clisting}

To avoid spending CPU cycles waiting for UART transmission to complete, the DMA buffers the character array directly to the peripheral. A flag, \cinline{txInProg}, prevents subsequent transmission until the UART transmit DMA callback, \cinline{HAL_UART_TxCpltCallback()}, clears the flag when the current transmission completes.
\begin{clisting}[caption={UART Transmit},label={list:uart_transmit}]
#define TX_BUFFER_MAX_LENGTH 2000 

uint8_t txBuffer[TX_BUFFER_MAX_LENGTH];
volatile uint8_t txInProg = 0;

// Transmit characters over UART
void transmitUART(char *ptr, int len)
{  
    // Check that the input isn't longer than our buffer
    if (len > TX_BUFFER_MAX_LENGTH){
        _Error_Handler(__FILE__, __LINE__);
    }
    // Wait until UART TX is finished
    while(txInProg == 1){}
    txInProg = 1;
    // Transfer the data to be sent into the txBuffer
    memcpy(txBuffer,(uint8_t *)ptr,len);
    HAL_UART_Transmit_DMA(&huart2, txBuffer, len); 
}

void HAL_UART_TxCpltCallback(UART_HandleTypeDef *huart)
{
    // Clear TX in progress flag when complete with transfer
    txInProg= 0;
}
\end{clisting}

\subsection{MCU Execution Flow}
The execution flow is as follows:
\begin{enumerate}
	\item Define and initialize a struct for motor pins and timer channels.
	\begin{clisting}[caption={Motor Struct},label={list:motor_struct}]
struct motor_t {
    GPIO_TypeDef *GPIOx;
    uint16_t GPIO_Pin;
    GPIO_PinState PinState;

    TIM_HandleTypeDef *TIM_Handle;
    TIM_OC_InitTypeDef sConfigOC;
    uint32_t TIM_Channel;
};

struct motor_t motorConfigs[4] = { 
    {MOTOR_FL_DIR_GPIO_Port, MOTOR_FL_DIR_Pin, GPIO_PIN_RESET, 0, {0}, TIM_CHANNEL_2}, 
    {MOTOR_FR_DIR_GPIO_Port, MOTOR_FR_DIR_Pin, GPIO_PIN_RESET, 0, {0}, TIM_CHANNEL_4}, 
    {MOTOR_BR_DIR_GPIO_Port, MOTOR_BR_DIR_Pin, GPIO_PIN_RESET, 0, {0}, TIM_CHANNEL_1}, 
    {MOTOR_BL_DIR_GPIO_Port, MOTOR_BL_DIR_Pin, GPIO_PIN_RESET, 0, {0}, TIM_CHANNEL_3}}; 
struct motor_t* motorConfigsPtr = motorConfigs;
	\end{clisting}
	\item Instantiate some variables.
	\begin{clisting}[caption={Communications Variables Initialization},label={list:comms_var_init}]
unsigned char data_packet[21];				// Holds sensor data for UART transmission
volatile uint8_t wd_reset = 0;				// Watchdog reset flag
volatile uint8_t sensor_update_req = 0;		// Queue rangefinder read flag
volatile uint8_t dbg_btn_latch = 0;			// Debug button latch
	\end{clisting}
	\item Enable all clocks since power saving not necessary.
	\begin{clisting}[caption={Enabling Clocks},label={list:enable_clocks}]
RCC->AHB1ENR |= 0xFFFFFFFF;
RCC->AHB2ENR |= 0xFFFFFFFF;
RCC->AHB3ENR |= 0xFFFFFFFF;
RCC->APB1ENR |= 0xFFFFFFFF;
RCC->APB2ENR |= 0xFFFFFFFF;
	\end{clisting}
	\item Reset peripherals, initialize SysTick, set up PLL and clocks.
	\begin{clisting}[caption={HAL and System Clock Initialization},label={list:hal_sysclk_init}]
HAL_Init();
SystemClock_Config();
	\end{clisting}
	\item Initialize configured peripherals.
	\begin{clisting}[caption={Peripheral Initialization},label={list:periph_init}]
MX_GPIO_Init();
MX_DMA_Init();
MX_I2C2_Init();
MX_I2C3_Init();
MX_TIM3_Init();
MX_TIM4_Init();
MX_TIM12_Init();
MX_USART2_UART_Init();
MX_TIM5_Init();
	\end{clisting}
	\item Reset system timer, enable UART receive DMA, initialize sensors.
	\begin{clisting}[caption={UART Service and Sensor Initialization},label={list:uart_sensor_init}]
TimeStamp_Reset();
serviceUART();
printf("Enabling IMU...\r\n");
IMU_begin();
printf("Initializing rangefinders...\r\n");
VL53L0X_begin();
	\end{clisting}
	\item Set servo to starting position.
	\begin{clisting}[caption={Servo Default Position},label={list:servo_default}]
if (HAL_TIM_PWM_Start(&htim12, TIM_CHANNEL_1) != HAL_OK){ Error_Handler(); }
	\end{clisting}
	\item Initialize variables and begin main loop.
	\begin{clisting}[caption={Loop Variables and Start},label={list:loop_start}]
uint32_t wd_start = 0;		// Watchdog start time
uint32_t cur_time = 0;		// Current time
uint8_t wd_en = 0;			// Watchdog enable
data_packet[20] = '\n';		// 21 byte sensor data packet to send over UART

while (1)
{
	\end{clisting}
	\item Watchdog prevents motors from running when UART is inactive. Receiving any UART command sets \cinline{wd\_reset} to 1.
	\begin{clisting}[caption={Motor Watchdog},label={list:motor_watchdog}]
	// Reset watchdog start time if flag is set
	if (wd_reset == 1){
		wd_start = TimeStamp_Get();  // Units of 0.1 ms based on Timer5
		wd_en = 1;
		wd_reset = 0;
	} else if (wd_en == 1){
		// Trigger if watchdog is enabled and expires
		cur_time = TimeStamp_Get();
		if ((cur_time - wd_start) > WD_LEN){
			wd_en = 0;
			
			// Disable motors
			int i;
			for (i=0; i<4; i++) {
				motorConfigs[i].PinState = GPIO_PIN_RESET;
				motorConfigs[i].sConfigOC.Pulse = 0; 
			}
			for (i=0; i<4; i++) {
				// Alter the PWM duty cycle and start PWM again
				if (HAL_TIM_PWM_ConfigChannel(motorConfigs[i].TIM_Handle, &motorConfigs[i].sConfigOC,
					motorConfigs[i].TIM_Channel) != HAL_OK) { Error_Handler(); }
				if (HAL_TIM_PWM_Start(motorConfigs[i].TIM_Handle, motorConfigs[i].TIM_Channel)
					!= HAL_OK){ Error_Handler(); }
				
				// Set the direction pin
				HAL_GPIO_WritePin(motorConfigs[i].GPIOx, motorConfigs[i].GPIO_Pin, motorConfigs[i].PinState);
			}
		}
	}											
	\end{clisting}
	\item Read debug tactile button state and latch it until read by UART.
	\begin{clisting}[caption={Debug Button Latch},label={list:dbg_btn_latch}]
	// Read debug button
	dbg_btn_latch = HAL_GPIO_ReadPin(B1_GPIO_Port, B1_Pin) && dbg_btn_latch;
	\end{clisting}
	\item If requested over UART, read all four rangefinders and store the data in the \cinline{data\_packet}.
	\begin{clisting}[caption={Rangefinder Read},label={list:range_read}]
	if (sensor_update_req == 1){
		int i;
		for (i = 0; i < 4; i++){
			if (rangefinderRead(i)){
				data_packet[i*2  ] = (rangeData[i] >> 8) & 0xFF;
				data_packet[i*2+1] =  rangeData[i]       & 0xFF;
			}
		}
		sensor_update_req = 0;
	}	
	\end{clisting}
	\item Read the magnetometer and store the data in the data packet.
	\begin{clisting}[caption={Magnetometer Read},label={list:mag_read}]
	magnetometer_read();
	data_packet[ 8] = (magData.x >> 8) & 0xFF;
	data_packet[ 9] =  magData.x       & 0xFF;
	data_packet[10] = (magData.y >> 8) & 0xFF;
	data_packet[11] =  magData.y       & 0xFF;
	data_packet[12] = (magData.z >> 8) & 0xFF;
	data_packet[13] =  magData.z       & 0xFF;	
	\end{clisting}
	\item Read the accelerometer and store the data in the data packet.
	\begin{clisting}[caption={Accelerometer Read},label={list:acc_read}]
	accelerometer_read();
	data_packet[14] = (accelData.x >> 8) & 0xFF;
	data_packet[15] =  accelData.x       & 0xFF;
	data_packet[16] = (accelData.y >> 8) & 0xFF;
	data_packet[17] =  accelData.y       & 0xFF;
	data_packet[18] = (accelData.z >> 8) & 0xFF;
	data_packet[19] =  accelData.z       & 0xFF;
}	
	\end{clisting}		
	\item Return to start of loop.
\end{enumerate}

\subsection{Error Handler}
During errors or faults, the MCU enters the error handler, prints an error message, and flashes the debug LED at 5 Hz.
\begin{clisting}[caption={Error Handler},label={list:error_handler}]
void _Error_Handler(char * file, int line)
{
	printf("Entered error handler.\r\n");
	while(1) 
	{
		HAL_GPIO_TogglePin(GPIOB, GPIO_PIN_1);
		HAL_Delay(100);
	}
}
\end{clisting}

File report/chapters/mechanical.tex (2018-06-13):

\chapter{Mechanical Design}
The robot meets the Roborodentia design requirements shown in Table \ref{tab:roborodentia_reqs}. It consists of four subassemblies: the base platform, shooting mechanism, ball hopper, and control unit. Each section was modeled in SolidWorks, an industry-standard solid modeling CAD program \cite{solidworks}. The parts were fabricated using a laser cutter or 3D printer and assembled with metric hardware. Figure \ref{fig:robot_photo} displays a photograph of the robot while Figures \ref{fig:render_isometric} through \ref{fig:render_right} show standard view renders of the SolidWorks model. Note that the robot uses mecanum wheels (a type of omni-directional wheel) \cite{ilon_1975} which are modeled as plain wheels for simplicity. Figure \ref{fig:render_top} also indicates the front, left, back/rear, and right sides of the robot. The robot contains 53 different mechanical components (including fasteners and off-the-shelf parts), of which 24 are custom designed, and 394 parts in total. The bill of materials can be found in Appendix \ref{appendix:mech_bom}.

\begin{table}[h]
	\caption{Roborodentia 2018 Mechanical Requirements}  \label{tab:roborodentia_reqs}
	\begin{tabularx}{\textwidth}{@{} c Y @{}}
		\toprule
		& Requirement \\ 
		\midrule
		1. & Maximum footprint of 12" x 14" or smaller at start of match but may expand up to 14" x 17" during match. \\
		2. & Maximum height of 14" at start of match but no restriction during match. \\ 
		3. & Robot may not disassemble into multiple parts. \\ 
		4. & Robot may not be airborne. \\ 
		5. & Shooting mechanisms may not accelerate balls past 50 feet per second. \\ 
		\bottomrule
	\end{tabularx} 
\end{table}

\begin{figure}[H]   % [h] means here
	\centering 
	\caption{Photograph of Robot}	\label{fig:robot_photo}
\end{figure}
\begin{figure}[H]   % [h] means here
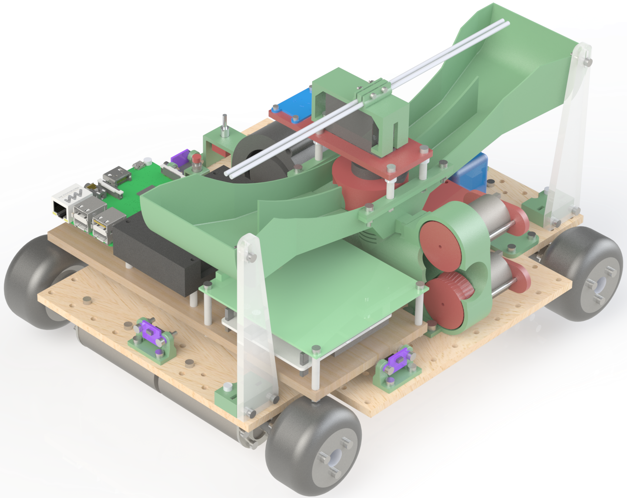
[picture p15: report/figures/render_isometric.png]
	\centering 
	\caption{Full Robot Render -- Isometric View}\label{fig:render_isometric}
\end{figure}
\begin{figure}[H]   % [h] means here
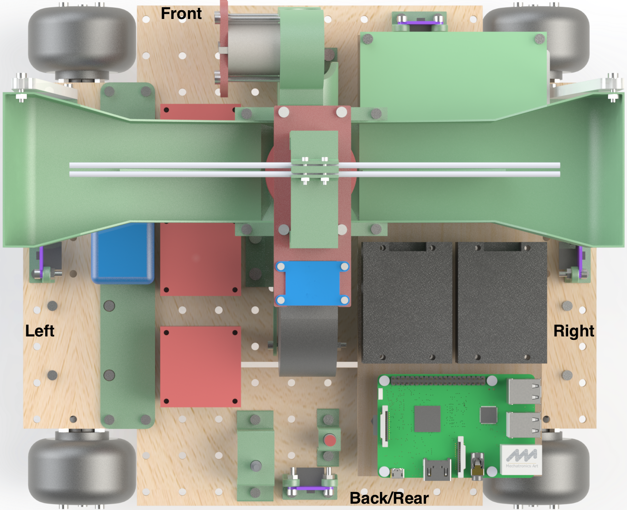
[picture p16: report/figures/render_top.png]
	\centering 
	\caption{Full Robot Render -- Top View}	\label{fig:render_top}
\end{figure}
\begin{figure}[H]   % [h] means here
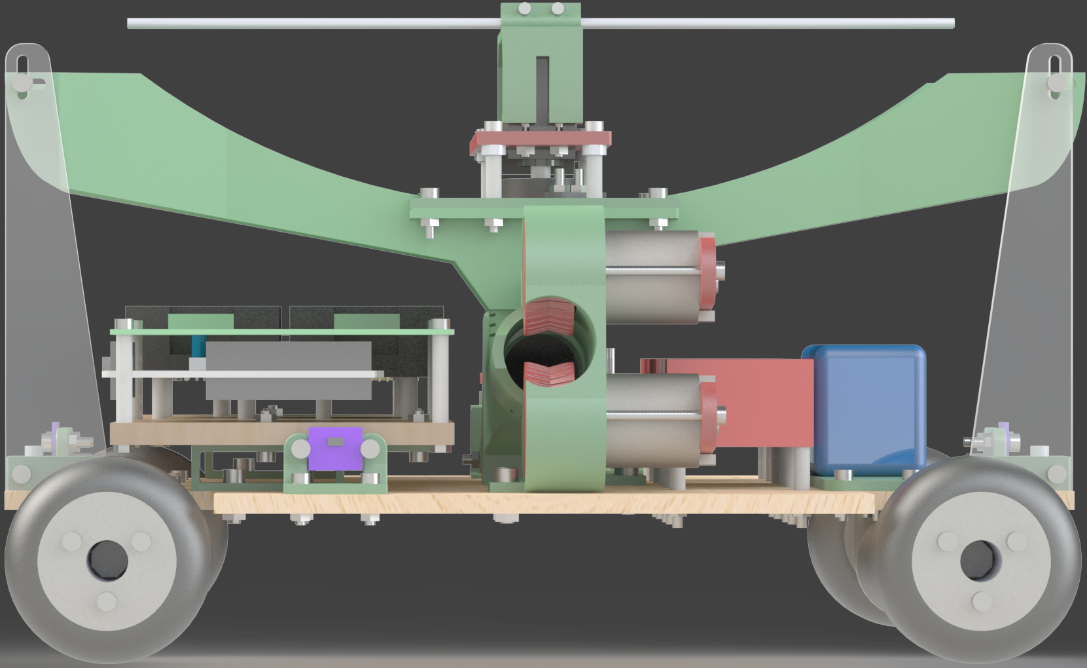
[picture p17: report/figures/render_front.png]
	\centering 
	\caption{Full Robot Render -- Front View}	\label{fig:render_front}
\end{figure}
\begin{figure}[H]   % [h] means here
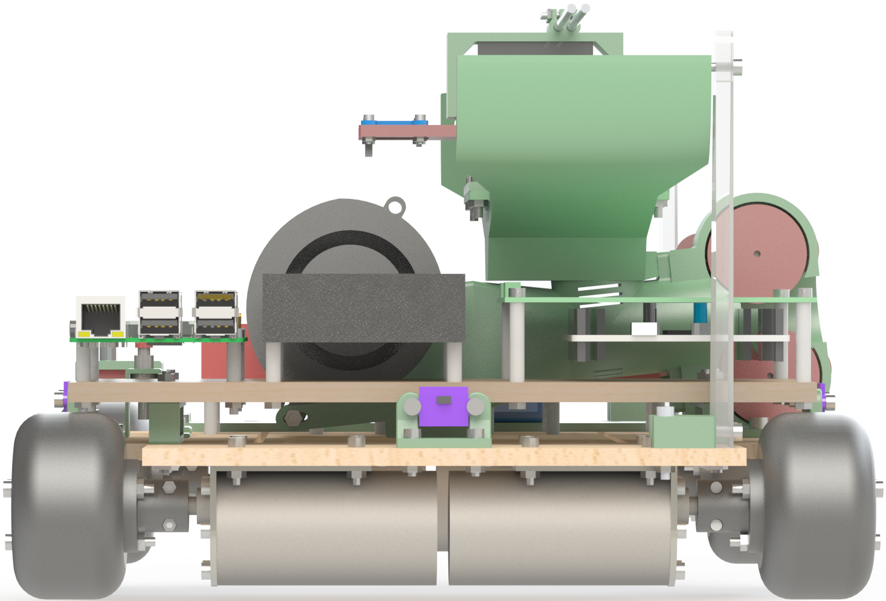
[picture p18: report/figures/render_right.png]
	\centering 
	\caption{Full Robot Render -- Right View}	\label{fig:render_right}
\end{figure}

The design emphasizes the use of 3D-printed parts to take advantage of the benefits of the technology including rapid part production, high part complexity, and low fabrication cost (excluding the cost of the printer, relative to other methods such as machining, casting, and injection molding), ideal for one-off part production. Parts were printed on a MakerGear M2 fused deposition modeling (FDM) 3D printer equipped with a 0.35 mm diameter nozzle using MakerGeeks 1.75 mm ABS thermoplastic filament \cite{makergear_m2}\cite{makergeeks}. Print speeds of 20 to 80 mm/s with 0.20 mm layer height, depending on part dimensions and minimum feature size, lead to part print times of 2--5 hours for smaller components and up to 26 hours for the ball hopper. Due to the non-isotropic strength characteristic of 3D-printed components, the designs must take into account printing direction and orientation. Parts tend to possess greater tensile strength in the X and Y axes but significantly less in the Z direction \cite{3dhubs_orientation}. Additionally, the print volume of 200 mm x 250 mm x 200 mm limits the maximum part dimensions, requiring the ball hopper to printed as three separate pieces \cite{makergear_m2}. 

\section{Base Platform}
The 315 mm x 275 mm base platform of the robot, made from 1/4" thick medium density fiberboard (MDF), serves as the primary structural component and mounting point for the motors, electronics, shooting mechanism, and hopper. The wood is laser cut with a 20 mm grid of 4 mm diameter holes to allow modular placement of components. The corner cutouts allow clearance for the wheels. Long slots permit wire routing from the motors to the motor drivers above. Figure \ref{fig:base_platform} shows the subassembly with labels.

\begin{figure}[H]   % [h] means here
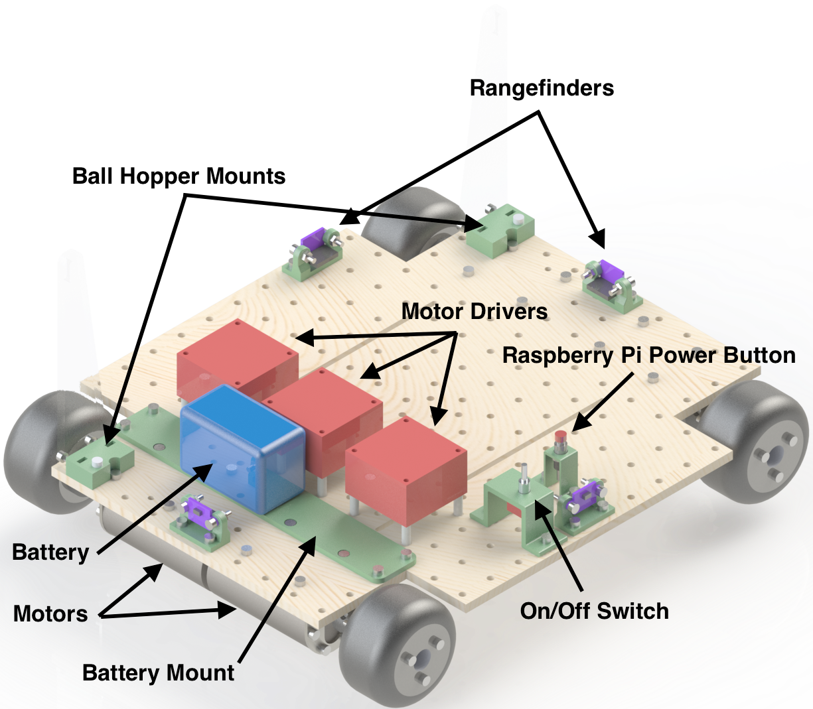
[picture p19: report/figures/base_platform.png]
	\centering 
	\caption{Base Platform}	\label{fig:base_platform}
\end{figure}

Four 12V Pololu 37D motors geared at a 70:1 ratio drive each of the 60 mm diameter mecanum wheels \cite{pololu}. Figure \ref{fig:motor_assem_explode} displays an exploded view of the motor assembly. 3D-printed couplings, detailed in Figure \ref{fig:wheel_coupler}, connect the wheels to the 6 mm diameter, D-shaped motor shafts. The couplers use M2 nuts and bolts to clamp onto the motor shaft and an octagonal stub that press fits into the center of the wheels. Three long M3 bolts and nylon lock nuts clamp the mecanum wheels together and to the coupler. Each wheel contains eight angled rollers mounted with two ball bearings each to smooth operation under load. Unlike regular wheels which only produce a force vector perpendicular to the axis, mecanum wheels also produce a vector parallel to the axis. With the appropriate combination of speed and direction of each wheel, the robot can achieve simultaneous translation and rotation in any direction. 

\begin{figure}[H]   % [h] means here
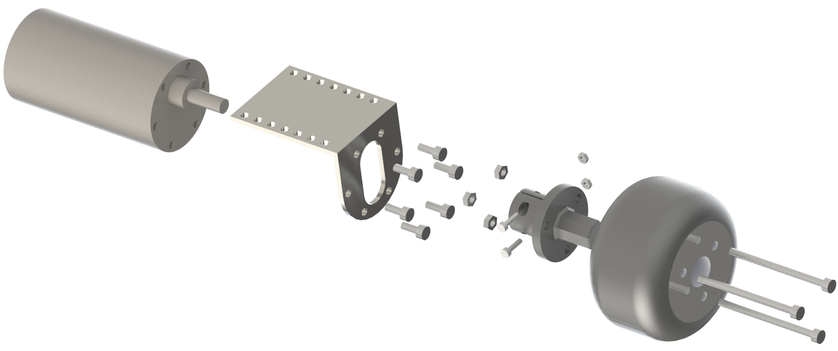
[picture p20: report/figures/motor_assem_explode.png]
	\centering 
	\caption{Motor Assembly Exploded View}	\label{fig:motor_assem_explode}
\end{figure}
\begin{figure}[H]   % [h] means here
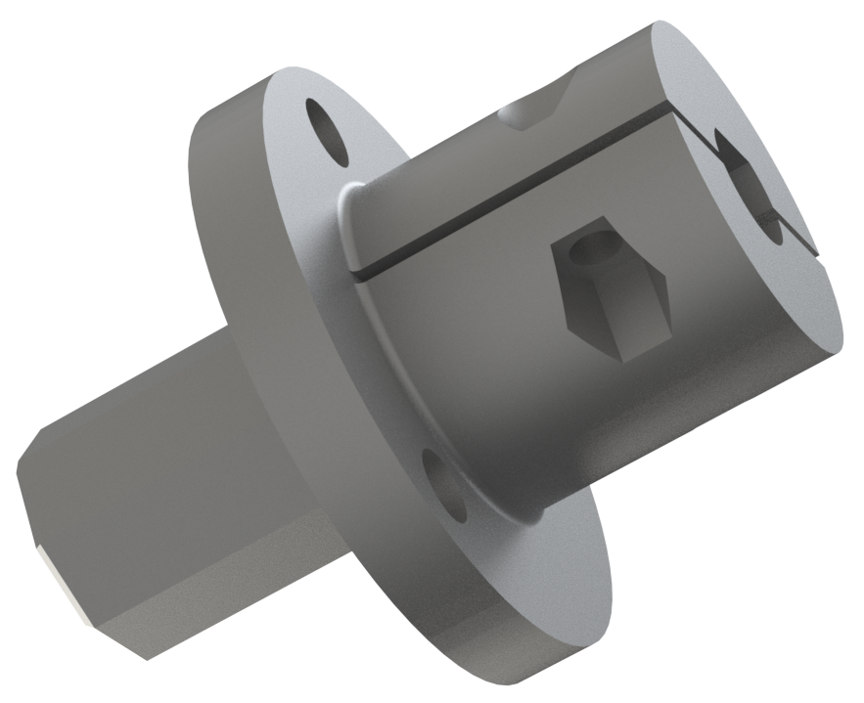
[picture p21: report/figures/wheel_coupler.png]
	\centering 
	\caption{Wheel Coupler}	\label{fig:wheel_coupler}
\end{figure}

Four STMicroelectronics VL53L0X laser rangefinders on the robot periphery sense distances between 30 mm and 2000 mm at a rate of 30 Hz and provide less than 10\% error in most test conditions \cite{vl53l0x_datasheet}. A 4S, 1800 mAH LiPo battery \cite{battery} mounted with an industrial strength hook-and-loop fastener powers the system through a on/off toggle switch seated in a 3D-printed bracket. Three dual H-bridge motor drivers are attached with nylon standoffs and M3 nuts and bolts. Finally, a momentary push button in a 3D-printed bracket toggles power to the Raspberry Pi microcomputer.

\section{Shooting Mechanism}
The competition calls for robots to fire Nerf Rival Balls into large nets positioned several feet away. The shooting mechanism takes inspiration from the official Nerf Rival Blaster toys since they're specifically optimized to fire Nerf Rival balls; the system works similarly to a baseball pitching machine. Figure \ref{fig:shooter_explode} shows an exploded view of the robot's shooter subassembly while Figure \ref{fig:shooter_top} displays the top view. The mechanism consists of two sections: the \textbf{barrel} and the \textbf{wheel housing}. Both parts were 3D-printed as the geometries are highly complex. Therefore, the shooting mechanism consists of two separate components versus a unibody design to allow each half to be fabricated with optimal print direction, strength, and finish quality. The barrel is angled \ang{6} above horizontal, targeting the vertical center of the nets 6 feet away.

\begin{figure}[H]   % [h] means here
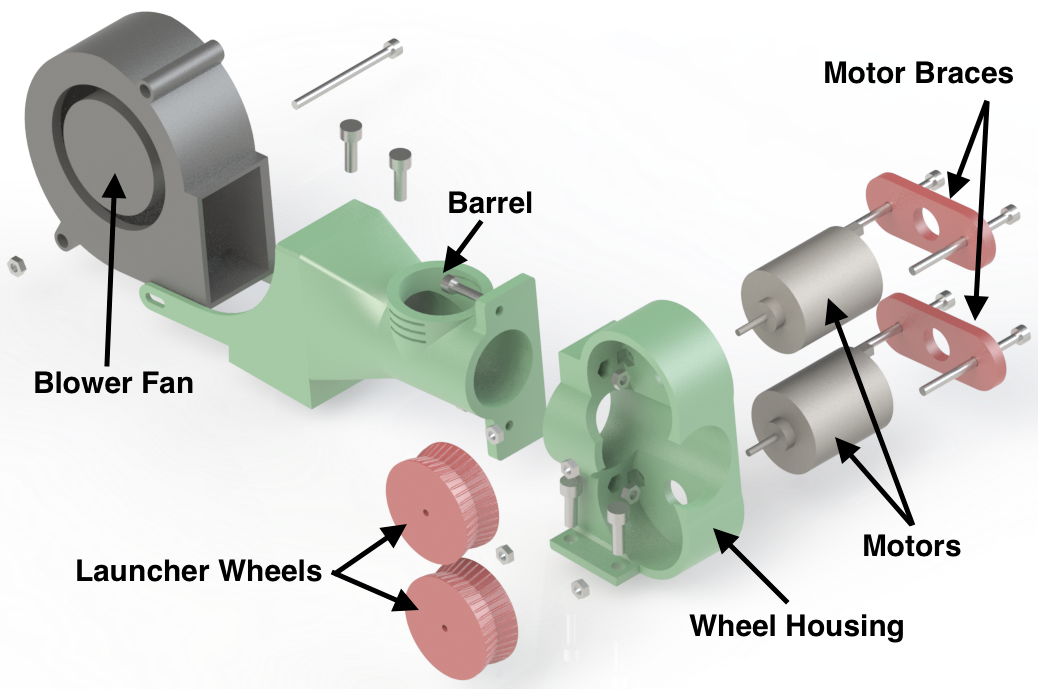
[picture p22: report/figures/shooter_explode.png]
	\centering 
	\caption{Shooting Mechanism -- Exploded View}	\label{fig:shooter_explode}
\end{figure}
\begin{figure}[H]   % [h] means here
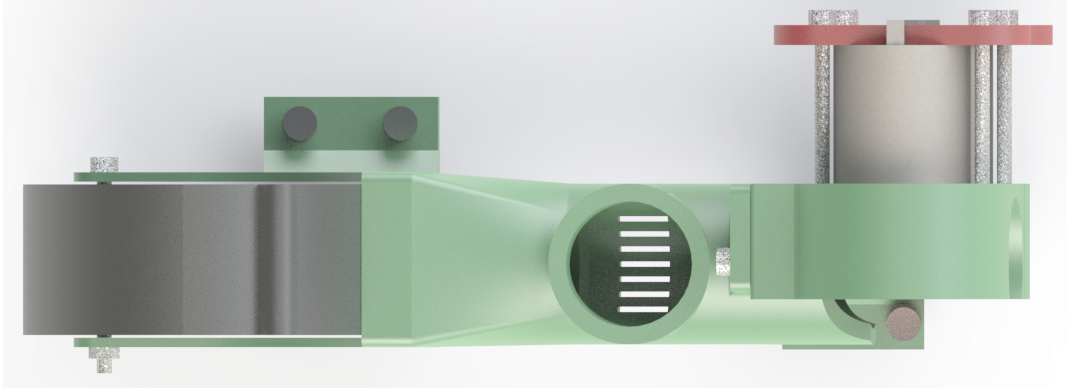
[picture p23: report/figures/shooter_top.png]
	\centering 
	\caption{Shooting Mechanism -- Top View}	\label{fig:shooter_top}
\end{figure}

The \textbf{barrel} directs balls from the \textbf{ball hopper} to the \textbf{wheel housing}. First, the ball enters the barrel through a vertical chute by force of gravity. As the ball falls into the barrel, a high-pressure centrifugal (or blower) fan attached at the back of the barrel pushes it into the wheel housing inlet. As seen in Figure \ref{fig:shooter_xsec}, the barrel slightly narrows in the area behind the top chute to prevent the ball from rolling backwards towards the blower fan. A 3D-modeling feature called a boss/base loft creates a smooth transition between the rectangular fan inlet and the circular barrel \cite{zuyderduyn_2016}. The foam balls, nominally 23 mm in diameter, would occasionally jam in a 24 mm inner diameter barrel due to ball surface imperfections, so the barrel was increased to 25 mm inner diameter. In the initial design, the pressure created by the blower fan was so high that it prevented the ball from falling down the vertical chute. The revised barrel uses strategically placed vents to reduce pressure before the ball enters the chute. As the ball travels down the chute into the barrel, it blocks the vents, increasing the pressure and forcing itself into the wheel housing.

\begin{figure}[H]   % [h] means here
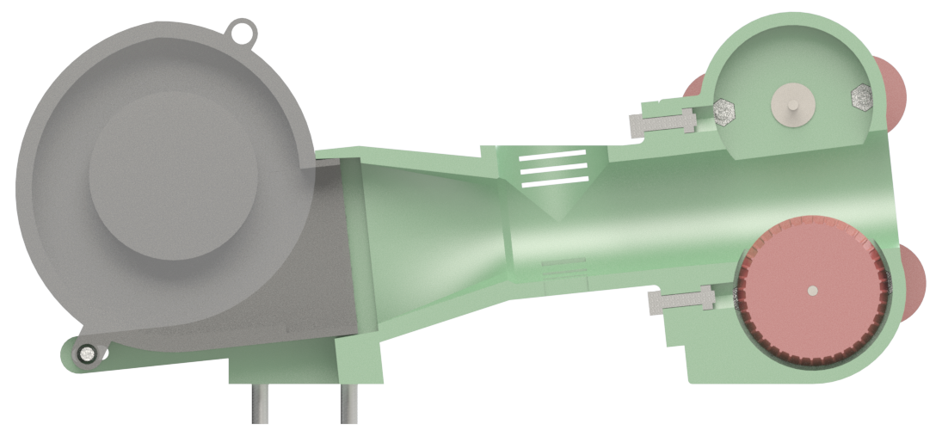
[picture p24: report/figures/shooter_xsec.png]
	\centering 
	\caption{Shooting Mechanism -- Cross Section View}	\label{fig:shooter_xsec}
\end{figure}

Inside the \textbf{wheel housing}, two counter-rotating 34mm wheels press fitted to two high-speed 12 V motors rapidly accelerate the foam ball up to 50 feet per second. The 14 mm gap between wheels compresses the ball to increase grip, thereby improving energy transfer. The motors lightly press fit into the wheel housing and are secured with 3D-printed braces. The perimeter of each 3D-printed wheel, detailed in Figure \ref{fig:shooter_wheel}, consists of a ribbed V-groove to increase the contact patch and grip with the compressed foam ball. Two ``feet'' with bolt holes at the bottom of the barrel and wheel housing secure the shooting mechanism to the base platform.

\begin{figure}[H]   % [h] means here
	\centering 
	\caption{Shooting Mechanism -- Shooter Wheel}	\label{fig:shooter_wheel}
\end{figure}

The shooting mechanism performed consistently: in a trial of 100 launches, 100\% of balls passed through a 6 inch diameter ring placed 6 feet away where the center of the competition net would be. Since the actual nets are 24 inches in diameter, no further testing was required. The projectile speed averaged 48.1 ft/s with 1.2 ft/s standard deviation as determined with a light gate speed measurement tool.

\section{Ball Hopper}
During the competition, the robot must obtain the foam Nerf balls from supply tubes mounted on either side of the play field. The supply tubes consist of two 1" inner diameter PVC tee joints and an eyebolt. The bottoms of the supply tubes are positioned seven inches above the floor and a swinging flap holds the balls in as shown in Figure \ref{fig:supply_tubes}. The ball hopper, shown in Figure \ref{fig:ball_hopper} is a large 3D-printed component designed to push the swinging flap away, collect the balls, store them, and dispense them into the shooting mechanism. Figure \ref{fig:ball_hopper_explode} shows an exploded view of the subassembly.

\begin{figure}[H]   % [h] means here
	\centering 
	\caption{Supply Tube}	\label{fig:supply_tubes}
\end{figure}
\begin{figure}[H]   % [h] means here
	\centering 
	\caption{Ball Hopper}	\label{fig:ball_hopper}
\end{figure}
\begin{figure}[H]   % [h] means here
	\centering 
	\caption{Ball Hopper -- Exploded View}	\label{fig:ball_hopper_explode}
\end{figure}

To obtain balls, the robot first positions itself such that the wide portion of hopper resides next to the supply tube. The robot then moves such that the metal rods at the top of the ball hopper push the eyebolt aside. As the flap swings open, the balls roll out of the supply tube and down the steep sloped portion of the hopper. Visible in the cross section view of Figure \ref{fig:ball_hopper_xsec}, the slope rapidly becomes shallower in order to convert the balls' downward momentum into sideways momentum which keeps balls from jamming against each other. The balls then roll into one of two channels before stopping at the dispensing gate.

\begin{figure}[H]   % [h] means here
	\centering 
	\caption{Ball Hopper -- Cross Section View}	\label{fig:ball_hopper_xsec}
\end{figure}

The dispensing gate, shown in Figure \ref{fig:dispensing_gate}, controls the movement of balls between hopper channels and the shooting mechanism entrance. Its complex shape directs balls into the hole at the bottom of the ball hopper from one channel at a time to prevent jamming. A standard \ang{180} rotation servo, mounted in a 3D-printed bracket above the center of the hopper, controls the dispensing gate.  Fastened to the same bracket, an inertial measurement unit (IMU) measures magnetic compass heading and acceleration in three dimensions for robot navigation purposes. The IMU is positioned at the rotational center of the robot to prevent the accelerometer from measuring robot rotation as linear movement. The ball hopper is mounted at three points: the top of the shooting mechanism and the left and right edges of the robot using 3D-printed and acrylic braces shown in Figure \ref{fig:hopper_brace}. 
\begin{figure}[H]   % [h] means here
	\centering 
	\caption{Ball Hopper -- Dispensing Gate}	\label{fig:dispensing_gate}
\end{figure}
\begin{figure}[H]   % [h] means here
	\centering 
	\caption{Ball Hopper -- Braces}	\label{fig:hopper_brace}
\end{figure}

\section{Control Unit}
The control unit, shown in Figure \ref{fig:control_unit}, consists of a 1/4" MDF board with various electronic components mounted: two off-the-shelf DC-DC switching converters, a custom interconnect printed circuit board (PCB), an off-the-shelf STM32 Nucleo-64 development board, and the Raspberry Pi microcomputer. Two 3D-printed standoffs, shown in Figure \ref{fig:control_unit_standoffs}, connect the control unit to the platform and raise it slightly to avoid colliding with the robot's wheels. 

\begin{figure}[H]   % [h] means here
	\centering 
	\caption{Control Unit}	\label{fig:control_unit}
\end{figure}

\begin{figure}[H]   % [h] means here
	\centering 
	\caption{Control Unit -- Standoffs}	\label{fig:control_unit_standoffs}
\end{figure}

\section{Results and Future Improvements}
The fabrication and assembly of the robot matched the 3D model and parts fit together as expected. Overall, the design can be improved through shrinking components by removing excess material. The close proximity of parts to each other made debugging and troubleshooting difficult.

Due to incomplete modeling of fasteners at the wheels, the base platform interfered slightly with the protruding bolt heads. Sanding the wheel cutouts corrected the issue. Otherwise, the base platform was largely successful. The grid of holes enabled easy relocation of components. Future designs may consider adding wheel suspension to improve traction.

The shooting mechanism underwent three revisions. The first used a belt and pulley system to allow a single slow motor to drive both high-speed launcher wheels, but the large footprint prevented compatibility with other robot components. The second revision was identical to the final iteration except for narrower barrel diameter and a pivot system to allow for aim angle adjustment. After discovering the ball jamming issue, the final iteration used a widened barrel diameter and a fixed aim angle. As described above, the final shooting mechanism was 100\% accurate in 100 trials and satisfied the competition speed limit. The design can be improved by modifying the barrel geometry to shrink the mechanism as it is still quite large.

The ball hopper used two revisions. The first revision used unnecessarily thick walls and extended the channel divider all the way to the edges of the hopper. It also used a shallower initial slope and a ball exit hole positioned in the center instead of offset. Balls would jam in the channel and refuse to fall down the center hole. The final design uses wider channels and a steeper slope to counter jamming problems. Future designs should consider using a single large ``bucket'' with an indexing agitator similar to the Geneva drive \cite{bickford_1972}.

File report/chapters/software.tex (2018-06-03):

\chapter{Software Design}

Placeholder.
%\section{Introduction}
%All of the software running on the off-robot computer is written in Python in order to take advantage of the ease of development, library selection, and the availability of TensorFlow, an open source machine learning framework critical to the neural network implementation. The Python scripts can be divided into five sections: robot interfacing, robot simulation, artificial neural network (ANN), deep deterministic policy gradient (DDPG) implementation, and utility functions. Table \ref{tab:script_desc} summarizes the functionality of the scripts.
%
%During development, the robot used either a 2015 MacBook Pro or desktop computer instead of the Raspberry Pi to simplify programming and omit limitations imposed by the Pi's lower processing speed.

%\begin{table}[h]
%	\caption{Software Functional Breakdown} 	\label{tab:script_desc}
%	\begin{tabularx}{\textwidth}{@{} r Y @{}}
%		\toprule
%		Functional Area & \multicolumn{1}{c}{Functionality} \\ 
%		\midrule 
%		Robot Interfacing 	& Establish serial link with microcontroller.  \\  
%							& Transmit UART commands. \\
%							& Receive and parse UART received data. \\
%							& Apply calibration constants to sensor data. \\
%							& Calculate tilt-compensated compass from IMU data. \\
%							& Store and update robot state (position, velocity). \\
%							& 
%							& dfjd \\ \addlinespace
%		Robot Simulation  	&  \\  
%							& dfjd \\ \addlinespace
%		ANN 				&  \\  
%							& dfjd \\ \addlinespace
%		DDPG 				&  \\  
%							& dfjd \\ \addlinespace
%		Utility 			&  \\ 
%							& dfjd \\
%		\bottomrule 
%	\end{tabularx} 
%\end{table}

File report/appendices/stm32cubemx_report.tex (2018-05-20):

\chapter{STM32CubeMX Report}
\label{appendix:stm32cubemx_report}
\includepdf[pages=-,pagecommand=\thispagestyle{plain}]{appendices/stm32cubemx_report.pdf}

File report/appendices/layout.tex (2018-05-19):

\chapter{Interconnect PCB Layout}
\label{appendix:layout}
\begin{figure}[H]   % [h] means here
	\centering 
	\caption{Interconnect PCB Layout -- Top Layer}\label{fig:pcb_layout_top}
\end{figure}
\begin{figure}[H]   % [h] means here
	\centering 
	\caption{Interconnect PCB Layout -- Bottom Layer}\label{fig:pcb_layout_bot}
\end{figure}

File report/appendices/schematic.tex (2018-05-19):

\chapter{Interconnect PCB Schematic}
\label{appendix:schematic}
\includepdf[pages=-,pagecommand=\thispagestyle{plain}]{appendices/schematic.pdf}

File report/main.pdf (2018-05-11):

ARTIFICIAL NEURAL NETWORK-BASED ROBOTICS

A Thesis

presented to

the Faculty of California Polytechnic State University,

San Luis Obispo

In Partial Fulfillment

of the Requirements for the Degree

Master of Science in Electrical Engineering

by

Justin Ng

June 2018

c 2018

Justin Ng

ALL RIGHTS RESERVED

ii

COMMITTEE MEMBERSHIP

TITLE: | Artificial Neural Network-Based Robotics
AUTHOR: | Justin Ng
DATE SUBMITTED: | June 2018
COMMITTEE CHAIR: | Andrew Danowitz, Ph.D.
| Assistant Professor of Electrical Engineering

COMMITTEE MEMBER: Xiao-Hua Yu, Ph.D.

Professor of Electrical Engineering

COMMITTEE MEMBER: Fred W. DePiero, Ph.D.

Professor of Electrical Engineering

iii

ABSTRACT

Artificial Neural Network-Based Robotics

Justin Ng

Artificial neural networks (ANNs) are highly-capable alternatives to traditional prob-

lem solving schemes due to their ability to solve non-linear systems with a non-

algorithmic approach. The applications of ANNs range from process control to pat-

tern recognition and, with increasing importance, robotics. This paper demonstrates

continuous control of a robot using an actor-critic algorithm based on deep determin-

istic policy gradients (DDPG) originally conceived by Google DeepMind. The robot

performs tasks such as locomotion within an enclosed area and object transporta-

tion. The paper also details the robot design process and explores the challenges of

implementation in a real-time system.

iv

ACKNOWLEDGMENTS

Thanks to:

- Everyone for everything.

v

TABLE OF CONTENTS

Page

CHAPTER

APPENDICES

vi

LIST OF TABLES

Table | Page

vii

LIST OF FIGURES

Figure | | Page
1.1 | Roborodentia Field | | 2

viii

Chapter 1

INTRODUCTION

Note: All project files can be found at https://www.github.com/okayjustin/

roborodentia2017 (https://www.github.com/okayjustin/roborodentia2017)

### 1.1 Definitions and Assumptions

The robot is designed to only travel within a rectangular closed area of eight feet in

the x direction and five feet in the y direction. The coordinate system is chosen as

Cartesian with the origin placed at the bottom-left corner of the field. The position of

the robot is always in the xy-plane since it cannot move vertically (z = 0). Therefore,

x refers to the robot position along the x-axis and ranges from 0 to 8 feet, and y refers

to position along the y-axis and ranges from 0 to 5 feet. Additionally, the robot can

only rotate around the z-axis so θ refers to the angle of the robot in the xy-plane.

Maintaining standard Cartesian coordinates, θ = 0◦
is along the positive x direction

while θ = 90◦
is along the positive y direction.

### 1.2 Cal Poly Roborodentia

The robot is designed to compete in the 2018 Cal Poly Roborodentia, the university’s

annual intramural robotics competition, and thus conforms to its particular specifica-

tions and requirements. Briefly, autonomous robots collect and fire Nerf Rival Balls

into nets to win points. A drawing of the field is shown below in Figure 1.1.


Figure 1.1: Roborodentia Field

Chapter 2

MECHANICAL DESIGN

Chapter 3

ELECTRICAL DESIGN

Chapter 4

FIRMWARE DESIGN

Chapter 5

SOFTWARE

### 5.1 Kalman Filters

The system relies on several different sensors to determine where it is within the

environment, a problem commonly referred to as robot localization. The Kalman

Filter (KF), an optimal state estimator, performs noise filtering and sensor fusion,

the process of combining measurements from multiple sensors. The filter operates

on the principles of Bayesian inference and uses statistically noisy measurements over

time and knowledge of the system to produce a more accurate estimate of an unknown

variable than with measurement alone.

### 5.1.1 Algorithm

The Kalman Filter algorithm and equations are reproduced here from Roger Labbe’s

excellent interactive online book [2]. The algorithm consists of two stages (not in-

cluding initialization): prediction and update. During the first stage, the filter uses

the current state and a process model (typically a function of time) to estimate the

state in the next time step along with its uncertainty. The second stage uses sensor

measurements to update the estimation by taking a weighted average based on the

ratio of uncertainty between the prediction and measurement.

Initialization

Before the first run of the filter, initialize the estimated state (x, also called the

posterior) and estimated state covariance matrix (P).

Predict

During the predict phase, the process model is used to predict the future state (known

as the prior) (¯x) after one time step by summing the posterior (x) multiplied by the

state transition function (F) with the control input model (B) multiplied by the

control input (u). The covariance of prior (P¯) is larger than the posterior covariance

(P) due to uncertainty in the process model (Q).

x¯ = Fx + Bu

P¯ = FPFT + Q

Update

Make measurements (z, measurement mean) and determine their accuracy (R, mea-

surement noise covariance). Calculate the residual (or difference) (y) between the

measurement and the product of the measurement function (H) and the prior from

the previous phase. H converts the prior from the state space to the measurement

space. Calculate the weighting factor (K, Kalman gain), valued between 0 and 1,

based on the whether the measurement or prior is more accurate. Set the new poste-

rior, x, to an average of the measurement and prior, weighted by K. Finally, update

the posterior’s covariance, P, based on the measurement certainty. The algorithm then loops back to the predict phase using the newly-calculated posterior.

y = z − Hx¯

K = PH¯ T

(HPH¯ T + R)
−1

x = x¯ + Ky

P = (I − KH)P¯

### 5.1.2 Design

The desired state variable x is chosen as the linear position, velocity, and acceleration

in the x and y directions as well as the angular position, velocity, and acceleration

about the z-axis:

x = [x y θ]

T

x˙ = [ ˙x y˙

˙θ]
T

x¨ = [¨x y¨

¨θ]
T

The process model for position and velocity:

x¯ = x + ˙x∆t + 0.5¨x(∆t)

2

x¯˙ = ˙x + ¨x∆t

x¯¨ = ¨x

Which can be written in the form:

x¯

x¯˙

x¯¨

=

1 ∆t 0.5(∆t)

2

0 | 1 | ∆t
0 | 0 | 1

x

x˙

x¨

x¯ = Fx

The measurement vector is chosen as:

z =

zx | zx¨ | zy | zy¨ | zθ | z ˙θ

T

The measurement noise matrix is shown below. The off-diagonals are 0 because the

noise between sensors is assumed to be uncorrelated.

R =

σ

2
x
| 0 | 0 | 0 | 0 | 0
0 | σ
| 2 x¨ | 0 | 0 | 0 | 0
0 | 0 | σ
| | 2 y | 0 | 0 | 0
0 | 0 | 0 | σ
| | | 2 y¨ | 0 | 0
0 | 0 | 0 | 0 | σ
| | | | 2 θ | 0
0 | 0 | 0 | 0 | 0 | σ

2
˙θ

Chapter 6

NEURAL NETWORK DESIGN

Chapter 7

CONCLUSION

BIBLIOGRAPHY

[1] J. Doe. The Book without Title. Dummy Publisher, 2100.
[2] R. R. Labbe. Kalman and bayesian filters in python, Sep 2017.
[3] R. Negenborn. Robot Localization and Kalman Filters. PhD thesis, Sep 2003.
[4] D. H. Nguyen and B. Widrow. Neural networks for self-learning control systems.

IEEE Control Systems Magazine, Apr 1990.

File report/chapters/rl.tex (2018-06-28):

\chapter{Reinforcement Learning}
The robot controls its motors using artificial neural networks (ANN) and the deep deterministic policy gradient (DDPG) algorithm, developed by Lillicrap et al.\ \cite{lillicrap_2016}. The system runs in Python 3 \cite{python3}, leaning heavily on the TensorFlow library with GPU support \cite{tensorflow} for artificial neural network instantiation, updating, and saving. After training, the system actuates each of the four drive motors to move the robot to a desired position and orientation in the Roborodentia field while minimizing the velocity and effort applied (i.e. energy spent). Two different approaches are implemented to compare DDPG performance with three separate single-output actors versus a single multiple-output actor. Before delving into the implementation and results, the following sections briefly cover reinforcement learning (RL) techniques that form the foundation of DDPG. It is worth noting that Sutton's introductory book on RL provides excellent background on many of the following algorithms and more \cite{sutton_2017}. 

\section{Reinforcement Learning Background}
Reinforcement learning (RL) is a subset of machine learning that aims to solve control and action selection problems rather than to perform classification or data clustering. In other words, the concern lies in determining which actions an actor should take in an environment to receive the greatest reward. Most reinforcement learning problems involve six main elements: an actor, the environment, rewards, a policy, a value function, and sometimes a model. An actor (sometimes called an agent) takes actions in an environment which returns a state and reward, illustrated in Figure \ref{fig:actor_env_loop}. The full state encompasses all the parameters of the environment and actor such as position, velocity, color, size, or any other measurable quantity; although the term ``state'' in this context refers to the subset of parameters observed by the actor. The actor's primary goal is to maximize the accumulated reward received from the environment. A policy determines which actions the actor takes given the current state. The value function indicates the long-term reward expected from a state and is defined for all possible states. To compare reward with value, even if a state only has a small immediate reward, it may possess high value since it leads to future high reward states. Finally, some algorithms involve a model of the environment, allowing prediction of the next state from the current state and action. Table \ref{tab:rl_defs} summarizes some common terms and definitions used in the reinforcement learning literature.
\begin{figure}[H]   % [h] means here
	\centering 
	\caption{Actor-Environment Feedback Loop}\label{fig:actor_env_loop}
\end{figure}
\LTXtable{\textwidth}{tables/tab_rl_defs.tex}

To better conceptualize these terms, consider a game of tic-tac-toe as shown in Figure \ref{fig:tictactoe}. The \textbf{environment} is the game itself, including the rules and game board. The two \textbf{actors} (players) sequentially take the \textbf{action} of placing marks in the boxes. The actions are encoded into some numeric form as defined by the designer. For example, $a=0$ might represent putting an X in the top left corner while $a=9$ might mean an X in the bottom right corner. Winning the game would grant a good \textbf{reward} while tying or losing might yield a bad reward. The reward could also come turn-by-turn instead of at the end of the game. Lining up marks for a win might produce a good reward while letting the opponent set a trap might be bad. The designer could even assign reward magnitudes to weight the significance of each state. Note that the descriptors ``good'' and ``bad'' are deliberately vague as numerous valid implementations of the reward exist. Conceptually, the reward allows the actor to differentiate between desirable and undesirable actions and states. No single ``correct'' reward implementation exists, but one should be chosen to reflect the desired policy. Each of the nine spaces can take one of three values (blank, X, or O) so the game has $3^9=19,683$ possible \textbf{states} (although some states are not achievable as the game would end once a player gets three in a row). Like the action, the rewards and states are represented numerically.
\begin{figure}[H]   % [h] means here
	\centering 
	\caption{A Game of Tic Tac Toe}\label{fig:tictactoe}
\end{figure}

\subsection{Long-Term Reward}
Actors strive to maximize the long-term discounted reward, $G_t$, where the subscript $t$ denotes the time step \cite{sutton_2017}. As mentioned previously, reward reflects the actor's policy. For example, the goal of tic tac toe is to win which, to the actor, is equivalent to taking actions that lead to states that lead to good rewards. In RL problems with a definitive end (denoted by $t=T$) such as a game of chess, $G_t$ is finite and can be calculated simply as the sum of all future rewards as shown in Equation \ref{eq:Gt_simple}. Additionally, the long-term aspect accounts for problems with intermediate rewards at each step. In chess, constantly trying to capture enemy pieces might yield some immediate good reward but may not actually be the best strategy for long-term success (i.e. winning the game).
\begin{equation}
	\label{eq:Gt_simple}
	G_t=R_{t+1}+R_{t+2}+\dots + R_{T}=\sum_{k=t}^{T-1} R_{k+1}
\end{equation}

However, continuous problems, such as maintaining the temperature of a refrigerator, have no maximum time step and therefore, a possibly infinite $G_t$. Shown in Equation \ref{eq:Gt_discount}, the introduction of a discount factor, $\gamma$, makes such a situation manageable. The discount factor weights the worth of future rewards exponentially by their distance into the future and ranges from 0--1 where 0 completely devalues future rewards while a discount factor of 1 weights all future rewards equally. In practice, the discount factor is less than 1 in order to allow $G_t$ to converge \cite{sutton_2017}. The discount factor can be considered a knob that sets the algorithm's outlook between myopic (short-sighted, only values immediate rewards) and far-sighted (willing to sacrifice immediate reward for greater long-term returns).
\begin{equation}
\label{eq:Gt_discount}
	G_t=R_{t+1}+\gamma R_{t+2}+\gamma^2 R_{t+3} + \dots = \sum_{k=0}^{\infty} \gamma^k R_{t+k+1}
\end{equation}

\subsection{Value Functions}
The \textbf{value} function $V_\pi(s)$ is the expected long-term reward $G_t$ as a function of the state $s$ under a certain policy $\pi$, written out in Equation \ref{eq:value_func}. The $\mathbb{E}_\pi$ operator evaluates the expected value provided the actor continues to take actions following policy $\pi$.
\begin{equation}
	\label{eq:value_func}
	V_\pi(s)=\mathbb{E}_\pi [G_t | s]
\end{equation}

Related but slightly different, the \textbf{Q-function} or \textbf{action-value} function $	Q_\pi(s,a)$ is the expected long-term reward $G_t$ as a function of the state $s$ \textbf{and action} $a$ under a certain policy $\pi$, shown in Equation \ref{eq:q_func}. The important distinction from the value function is dependency on the action. While the value function describes the expected long-term reward from being in a particular state and continuing to follow actions under the policy $\pi$, the Q-function returns the expected long-term reward from being in a particular state, taking a specific action, then continuing to follow actions under the policy $\pi$. Since the Q-function uses three variables ($s$, $a$, and $Q$), it can be plotted in three dimensions as in Figure \ref{fig:q_ex_plot}. Note that this is arbitrary plot for demonstration purposes more than representing actual Q-values for any particular environment. 

Considering tic tac toe, if $s=0$ represents the starting, i.e. blank, state of the game, the red slice of Figure \ref{fig:q_ex_plot} would represent the Q-values or expected long-term reward for each of the nine possible starting actions. Likewise, every slice would represent Q-values for the various actions taken in other game states, and the plot would have as many slices as there exist game states. Again, note that this is only an example and not the actual plot of tic tac toe's Q-function; it would use discrete points rather than the continuous function shown. The Q-function is defined for all possible states and actions so tic tac toe contains $19,683 \text{ states} \cdot 9 \text{ actions} = 177,147$ discrete Q-values. Notice that the Q-function is non-obvious, highly non-linear, and may be continuous or discrete depending on the specific problem.
\begin{equation}
	\label{eq:q_func}
	Q_\pi(s,a)=\mathbb{E}_\pi [G_t |s,a]
\end{equation}
\begin{figure}[H]   % [h] means here
	\centering 
	\caption{3D Q-Function Example}\label{fig:q_ex_plot}
\end{figure}

\subsection{Policies}
Various policies exist but some of the most common include optimal, greedy, $\epsilon$-greedy, and random. The optimal policy $\pi_*$, by definition, produces greater or equal value for every possible state than any other policy $\pi$, expressed in Equation \ref{eq:optimalpol}, where $v_{\pi_*}$ represents the value function of the optimal policy, $v_{\pi}$ is the value function of any other policy $\pi$, and $\mathcal{S}$ is the set of all possible states. Ideally, the actor would eventually discover the optimal policy, but in reality, training always produces a sub-optimal policy except for the simplest of environments. 
\begin{equation}
	\label{eq:optimalpol}
v_{\pi_*}(s) \geq v_{\pi}(s), \forall s \in \mathcal{S}
\end{equation}
An actor under the random policy always takes random actions while the greedy policy directs the actor to take the action with the highest value or Q-value depending on implementation. Although greediness does lead the actor to take actions that it believes maximize the reward, it may also cause the actor to get stuck following a suboptimal policy. For example, if a greedy actor is learning tic tac toe, it may discover that putting an X in the middle of the top row as the first move led it to win. Being greedy, it will keep putting the mark there since it sometimes leads to a reward. However, if the actor would stop being greedy and try something new, it would eventually discover that putting the first mark in a corner leads to victory more often. In other words, an actor following a greedy policy may not sufficiently explore the environment, i.e. try new things to discover better actions or states which lead to even greater reward. To allow a balance between exploration (discovering better rewards) and exploitation (obtaining as much reward as it can), the $\epsilon$-greedy policy tells an actor to pick the greedy action with probability $1-\epsilon$ and a random action with probability $\epsilon$ where $\epsilon$ ranges between 0 and 1. 

\section{Reinforcement Learning Algorithms}
Many reinforcement learning algorithms have been applied to action selection and control problems including Q-Learning, State-Action-Reward-State-Action (SARSA), deep Q-network (DQN), policy gradients (PG), deep policy gradients (DPG), and deep deterministic policy gradients (DDPG), among others \cite{sutton_2017}\cite{sutton_policygrad}\cite{silver_2017}\cite{silver_lever_heess_degris_wierstra_riedmiller}\cite{lillicrap_2016}. Note that these methods differ from evolutionary algorithms in that they actively learn as they interact with the environment. Instead, evolutionary techniques evaluate the performance of individual actors in a population by determining how much reward each produces while operating in the environment, take the best performers, mutate them slightly to produce new behaviors, and repeat until a good policy emerges. The process is highly reminiscent of natural selection while the algorithms to be discussed are more akin to a child learning to walk \cite{natural_selection}.

RL algorithms can be classified by their use of models (model-based vs.\ model-free) and actor policy (on-policy vs.\ off-policy) \cite{sutton_2017}. Model-based strategies first develop a model of the environment and then use a planning algorithm along with the model to create a controller, while model-free algorithms forgo the model entirely. On-policy strategies learn the policy followed by the actor while off-policy techniques learn a policy different from the one followed by the actor. For example, in Q-learning, the Q-function updates its weights based on the next state and the greedy action (which is not actually executed) even if the actor is following the random policy \cite{sutton_2017}. The greedy action is determined by searching the Q-function in the next state for the action producing the highest Q-value, further explained in the Q-Learning section.

\subsection{Q-Learning}
Q-Learning is an off-model, off-policy algorithm that estimates the Q-function of the environment \cite{sutton_2017}. The Q-function represents the ``quality'' of every possible action in every possible state. Given a particular state, the Q-function returns the quality, i.e.\ predicted goodness, of each possible action the player could take. Therefore, the optimal action to take is simply the one with the highest Q-value. 

Clearly, the Q-function always exists but not necessarily in an analytic or obvious form. So-called tabular Q-learning methods use a 2-D matrix to represent the Q-function with rows for all possible states and columns for all possible actions \cite{mccullock}. The table is initialized with guesses (possibly randomly or with all elements set to 0) and iteratively updated to produce an approximation closer and closer to the true Q-function $Q^*$ using the Bellman equation presented in Equation \ref{eq:bellman}. The equation states that the expected long-term reward Q for state $s$ and action $a$ is equal to the reward received from being in state $s$ plus the discounted ($\gamma$) maximum Q of the next state $s'$. In simpler terms, the expected long-term reward is the current state's reward plus the best reward obtainable in the next state (weighted by $\gamma$). For clarity, the $\text{max}_{a'}(\cdot)$ operator chooses $a'$ to maximize its argument $(\cdot)$ so $\text{max}_{a'}(Q(s',a'))$ means the maximum Q of the next state $s'$ irrespective of the action $a'$. The proof that the Bellman equation does allow iterative Q-value calculation is beyond the scope of this thesis, but Sutton's book, \textit{Reinforcement Learning: An Introduction}, provides further explanation \cite{sutton_2017}.
\begin{equation}
	\label{eq:bellman}
	Q(s,a)=R(s) + \gamma (\text{max}_{a'}(Q(s',a')))
\end{equation}

To improve convergence, i.e. when the estimated Q-function approaches the optimal $Q^*$, Equation \ref{eq:bellman} is modified to include the learning rate $\alpha$, ranging between 0 and 1, which reduces the change in the Q-function with each iteration, shown in Equation \ref{eq:bellman_alpha}. The pseudocode for Q-learning presented by Sutton is reproduced in Table \ref{list:qlearning_pseudo} with permission. Some environments, like chess, eventually terminate (at the end of the game) while others, such as maintaining a refrigerator's temperature, may never actually terminate.
\begin{equation}
	\label{eq:bellman_alpha}
	Q(s,a)=(1-\alpha)Q(s,a) + \alpha[R(s) + \gamma (\text{max}_{a'}(Q(s',a')))]
\end{equation}
\begin{clisting}[caption={Q-Learning Pseudocode},label={list:qlearning_pseudo}]
Initialize Q(s,a) arbitrarily. 
Repeat for each episode: 
	Initialize s
	Repeat for each step of episode:
		Choose a from s using policy derived from Q (e.g., epsilon-greedy)
		Take action a, observe r, s'
		Q(s,a) = (1 - alpha) * Q(s,a) + alpha * [r + gamma * max_a(Q(s',a'))]
		s = s';
	until s is terminal 
\end{clisting}

Notice the algorithm recursively updates the Q-value, $Q(s,a)$, from the Q-value of the next state and greedy policy action, $\text{max}_{a'}Q(s',a')$, regardless of the policy and action taken by the actor. This characteristic makes Q-learning an off-policy algorithm. The Q-value for a particular state and action only updates when the actor visits said state and action so the actor must still explore (i.e.\ not always take greedy actions) for Q-learning to converge. Figure \ref{fig:q_learning_ex} illustrates an example of one step of recursive Q-function update using the tic tac toe. 
\begin{figure}   % [h] means here
	\centering 
	\caption{Tabular Q Update Example}\label{fig:q_learning_ex}
\end{figure}

Clearly, the tabular Q method quickly becomes unfeasible for more complex problems, especially when the states or actions are continuous rather than discrete. When the action or state spaces are continuous, the algorithm must discretize them, forcing a tradeoff between resolution and tractability. For the tic-tac-toe example, the table would be 19,683 rows by 9 columns for a total of 177,147 Q-values while the Q-value table for a game of chess would possess more elements than there are atoms in the known universe. Hence, methods such as the yet-to-be-discussed Deep Q-Network Method represent the Q-function using other structures like artificial neural networks.

\subsection{State-Action-Reward-State-Action (SARSA)}
SARSA is an on-policy algorithm which shares many characteristics with Q-learning \cite{sutton_2017}. The name comes from the fact that the Q update equation uses the current \textbf{s}tate and \textbf{a}ction as well as the next \textbf{r}eward, \textbf{s}tate, and \textbf{a}ction. The pseudocode for SARSA presented by Sutton is reproduced in Table \ref{list:sarsa} with permission.
\begin{clisting}[caption={SARSA Pseudocode},label={list:sarsa}]
Initialize Q(s,a) arbitrarily. 
Repeat for each episode: 
	Initialize s
	Choose a from s using policy derived from Q (e.g., epsilon-greedy)
	Repeat for each step of episode:
		Take action a, observe r, s'
		Choose a' from s' using policy derived from Q (e.g., epsilon-greedy)
		Q(s,a) = (1 - alpha) * Q(s,a) + alpha * [r + gamma * Q(s',a')]
		s = s'; a = a';
	until s is terminal 
\end{clisting}

Unlike Q-learning, SARSA updates Q-values from the next state and next action $Q(s',a')$, making it an on-policy strategy. Like Q-learning, the actor must take exploratory actions for the algorithm to update Q at all states and actions and achieve convergence.

\subsection{Deep Q Network (DQN)}
Deep Q Networks, developed by Mnih et al. \cite{Mnih_2015}, aim to solve two significant problems with Q-learning and SARSA: the inability to handle situations with large state and action spaces and the inability to generalize learnings to new situations \cite{sutton_policygrad}. As mentioned previously, maintaining Q-values for the entire state and action space of a complex problem requires enormous memory. The second problem has to do with how the Q-value table updates. In both Q-learning and SARSA, the algorithms iteratively update Q-values for visited (state, action) pairs. However, to fully update the Q-value table means exploring every possible state and action combination multiple times, a non-trivial task. In other words, the algorithms cannot provide reasonable Q-value estimates for unvisited situations.

To overcome these limitations, DQN replaces the tabular Q concept with an artificial neural network (ANN) where the inputs are the state and action and the output is the Q-value. The Q-network is denoted as $Q(s,a;\theta_i)$ where $\theta_i$ represents the network weights. The loss function, displayed in Equation \ref{eq:dqn_loss_func}, is the squared error between the Q-network output and the ``target Q-value'' as defined by the Bellman equation, $y_j = r + \gamma \text{max}_{a'}Q(s', a';\theta^-_i)$  \cite{Mnih_2015}. For complete clarity, $Q(s,a;\theta^-_i)$ represents an identical but separate copy of Q-network $Q(s,a;\theta_i)$ except with weights $\theta^-_i$ from a previous iteration, explained later.
\begin{equation}
	\label{eq:dqn_loss_func}
L_i(\theta_i) = (r + \gamma \text{max}_{a'}Q(s', a';\theta^-_i)-Q(s,a;\theta_i))^2
\end{equation}

To assist DQN training, Mnih et al.\ used a technique called experience replay \cite{Mnih_2015} As the actor explores within environment, the algorithm records transitions consisting of the current state, action taken, reward, and next state at each time step into a so-called experience replay buffer. After collecting a minimum number of experiences, the artificial neural network trains from data sampled randomly from the buffer, hence the name ``experience replay''. The technique removes time correlations in the training data, improves convergence, and also allows experience reuse, advantageous when obtaining data is difficult or costly. In the context of ANNs, convergence refers to when the ANN output approaches the function being approximated by the network.

The second technique Mnih et al.\ used to counter training instability, i.e. when the network weights oscillate instead of settling, involves generating target Q-values, $y_j$, from an identical but separate ANN, called the target Q-network $\hat{Q}$ with weights $\theta^-_i$. In effect, this creates a time delay between when the weights of $Q$ are updated and when those updates affect the policy and target Q-network, reducing the likelihood of policy instability. For example, using a size 64 mini-batch, the network randomly samples 64 transitions from the experience replay buffer and trains the network $Q$ with 64 iterations as in Equation \ref{eq:dqn_loss_func}. After, the target network $\hat{Q}$ clones the weights $\theta_i$ from $Q$ and the process repeats.

The DQN method replaces the tabular Q with an artificial neural network to solve RL problems with large Q spaces. However, the algorithm's policy still uses a discrete action space, posing a problem for situations requiring continuously variable actions. For example, a system with five continuous actions discretized into a mere four bits each already produces $(2^4)^5=1,048,576$ different action combinations. Policy gradient methods can overcome this limitation as described next.

\subsection{Stochastic Policy Gradient Method}
Q-Learning, SARSA, and DQN are value-based methods as they rely on finding the environment's underlying Q-function and produce a policy to maximize Q. Policy gradient methods find the optimal policy directly, making them policy-based strategies \cite{sutton_policygrad}. DeepMind's AlphaGo demonstrated PG's viability by famously defeating grandmaster Go player Fan Hui in 2015 and Lee Sedol in 2016 \cite{silver_2017}.

The core of the policy gradient method is the parametrized probabilistic action distribution $P[a|s;\theta]$. Essentially, the distribution defines the probability of taking any particular action in the set of all possible actions for a particular given state $s$. For example, if an actor has three possible actions, they might occur 10\%, 30\%, and 60\% of the time, respectively. However, since $P[a|s;\theta]$ is continuous, the policy would produce continuous-valued actions rather than three discrete ones. The parameters $\theta$ adjust the distribution's shape and therefore the likelihoods of each action. 

The underlying premise of stochastic policy gradients is simple: get a state, take a particular action picked stochastically from probability distribution $P[a|s;\theta]$, and record the reward. If the reward is ``good'', increase the probability of taking that action by modifying $\theta$ or decrease it if the reward is ``bad''.\footnote{Note that the terms ``good'' and ``bad'' are intentionally vague as to not constrain them to one particular interpretation.} After many iterations, the actor will most likely take actions that produce good rewards. But of course, not all is so simple. Much like the so-called ``butterfly effect'' \cite{Lorenz_1963}, a single action can cascade into a multitude of unknown futures meaning the worth of a particular action cannot be determined by the immediate reward produced.

Instead, the rewards are accumulated for a long period in episodes, at the end of which actions are judged based on the total reward. Now, a different issue arises: the credit assignment problem \cite{fu_2008}. If an episode contains 1,000 actions, which ones ultimately produced the good reward and which were inconsequential or detrimental? Rather than determining the individual ones responsible, the algorithm deems all the actions in the episode culpable so if the episode's outcome is good, all actions taken become more likely and if not, the inverse occurs \cite{karpathy_2016}. Like AlphaGo, many policy gradient implementations use an artificial neural network to represent the action probability distribution where the inputs are states and outputs are action probabilities \cite{silver_2017}. Therefore, the act of making actions more or less probable is carried out with gradient descent similar to back propagation for ANNs \cite{karpathy_2016}. However, the specific implementation details are beyond the scope of the thesis.

\subsection{Deterministic Policy Gradient Method (DPG)}
The deterministic policy gradient method (DPG), developed by Silver et al., shares the same foundation as stochastic policy gradients, but instead of representing the policy as a probability distribution, the policy deterministically chooses an action given a particular state \cite{silver_lever_heess_degris_wierstra_riedmiller}. Silver et al.\ have shown that the DPG is actually a limiting case of stochastic policy gradients where the policy distribution variance is 0. Another key difference is that while the stochastic policy gradient integrates over the state and action spaces, the DPG only integrates over the state space. Consequently, the stochastic case requires more samples to compute. Specific details can be found in the original paper. Finally, while the stochastic policy inherently chooses exploratory actions due to its probabilistic nature, the deterministic case is more akin to a greedy policy. Therefore, Silver developed an off-policy learning algorithm using a stochastic policy to ensure sufficient exploration despite producing a deterministic policy.

\subsection{Deep Deterministic Policy Gradient (DDPG)} \label{sec:ddpg}
The robot's motors are controlled with continuous actions so the policy gradient method provides a decent solution. However, PG methods converge more slowly and have less learning stability than the DQN algorithm, as compared in Table \ref{tab:dqn_pg_comparison} \cite{yu_dqn_vs_pg}. Therefore, the deep deterministic policy gradient (DDPG), developed by Lillicrap et al., augments the DPG algorithm with techniques from DQN to obtain the best of both worlds.

\begin{table}[h]
	\caption{DQN and PG Comparison \cite{yu_dqn_vs_pg}}  \label{tab:dqn_pg_comparison}
	\begin{tabularx}{\textwidth}{@{} l|c|c @{}}
		\toprule
		& Deep Q-Network Method & Policy Gradient Method \\ 
		\midrule
		Policy Action Space & Discrete & Continuous \\
		Policy State Space & Continuous & Continuous \\
		Q-Function Action Space & Continuous & n/a \\
		Q-Function State Space & Continuous & n/a \\
		Learning Stability & More Stable & Less Stable \\
		Convergence Speed & Faster & Slower \\
		\bottomrule
	\end{tabularx} 
\end{table}

The DDPG algorithm is a model-free, off-policy actor-critic strategy based on Silver et al.'s DPG algorithm combined with learnings from Mnih et al.'s work on the DQN algorithm \cite{lillicrap_2016}\cite{Mnih_2015}\cite{silver_lever_heess_degris_wierstra_riedmiller}. DDPG improves on DPG by representing the actor's policy with an ANN and applying the experience replay and target network techniques from DQN. The actor-critic architecture, shown in Figure \ref{fig:actor_critic}, uses techniques from policy-based methods (find the policy directly) as well as value-based methods (estimate Q-function) \cite{actor_critic}. Each DDPG network uses an ANN for the actor and critic each plus another two for the target networks for a total of four ANNs. 
\begin{figure} [h] %means here
	\centering 
	\caption{Actor-Critic Architecture}\label{fig:actor_critic}
\end{figure}

The two major steps in any actor-critic method are actor improvement and critic evaluation \cite{actor_critic}. During actor improvement, the Q-values (more specifically, the gradient thereof) produced by the critic are used to train the actor network to better follow the policy. During critic evaluation, the critic, which is really just a Q-approximator as implemented in DQN, is improved using the Bellman equation. Conceptually, the actor and critic are much like a basketball player and coach. The coach learns the game and comes up with a strategy while the player focuses on executing the plan as best as possible.

Additionally, Lillicrap et al.\ adapted batch normalization from Ioffe's work to allow ANN hyper-parameter generalization for environments with features of varying magnitude \cite{2015arXiv150203167I}; each feature in a minibatch is normalized to unit mean and variance. In other words, the DDPG algorithm can use the same set of hyper-parameters, e.g. learning rates, discount factor, update parameter $\tau$, etc., for widely different environments. In their implementation, batch normalization was applied to network inputs, all layers of the policy network, and all layers of the Q network before the action input (detailed later).

To ensure adequate exploration, Lillicrap et al.\ added Ornstein-Uhlenbeck process noise to the policy output $\mu(s_t | \theta^\mu_t)$ to create the exploration policy $\mu'(s_t)$ as shown in Equation \ref{eq:exploration_policy} \cite{lillicrap_2016}. The Ornstein-Uhlenbeck process satisfies the condition shown in Equation \ref{eq:ornstein-uhlenbeck} where $x_t$ is the process position at time $t$, $\theta$ and $\sigma$ are parameters, and $W_t$ is the Weiner process \cite{uhlenbeck_ornstein}. The process produces random, time-correlated values that drift toward a long-term mean, in this case 0. The Ornstein-Uhlenbeck action noise class shown in Listing \ref{list:ornstein-uhlenbeck} is provided by OpenAI under the MIT License \cite{ddpg_noise}.
\begin{equation}
\label{eq:exploration_policy}
\mu'(s_t) = \mu(s_t | \theta^\mu_t) + \mathcal{N}
\end{equation}
\begin{equation}
\label{eq:ornstein-uhlenbeck}
dx_t = \theta(\mu-x_t) dt + \sigma dW_t, \theta>0, \sigma>0
\end{equation}

Lillicrap et al.\ used DDPG to solve over 25 different simulated physics environments such as cart pole swing-up and driving using the same network architecture and hyper-parameters, demonstrating the generalizability of the technique. For details of the environments, see OpenAI Gym \cite{openaigym}. Although the approach required about 2.5 million steps of experience to solve most problems, this represents 20 times less than DQN while still providing better performance in most cases.

To reiterate, the important advantage of the DDPG technique is its ability to handle both continuous action and state spaces of varying magnitude, critical to many real-life control problems. Specific algorithm details are covered in the Implementation section.

\begin{python}[caption={Ornstein-Uhlenbeck Action Noise \cite{ddpg_noise}},label={list:ornstein-uhlenbeck}]
class OrnsteinUhlenbeckActionNoise:
    def __init__(self, mu, sigma=0.3, theta=.15, dt=0.05, x0=None):
        self.theta = theta
        self.mu = mu
        self.sigma = sigma
        self.dt = dt
        self.x0 = x0
        self.reset()

    def __call__(self):
        x = self.x_prev + self.theta * (self.mu - self.x_prev) * self.dt + \
                self.sigma * np.sqrt(self.dt) * np.random.normal(size=self.mu.shape)
        self.x_prev = x
        return x

    def reset(self):
        self.x_prev = self.x0 if self.x0 is not None else np.zeros_like(self.mu)

    def __repr__(self):
        return 'OrnsteinUhlenbeckActionNoise(mu={}, sigma={})'.format(self.mu, self.sigma)
\end{python}

\section{Implementation}
All code is implemented in Python 3.6 and uses modules from TensorFlow \cite{tensorflow} (ANN implementation), OpenAI Gym (Ornstein-Uhlenbeck action noise) \cite{openaigym}, and Pyglet (environment rendering). An implementation of Lillicrap's DDPG algorithm from Patrick Emami's reinforcement learning primer formed the initial code base to which modifications and new developments were added \cite{emami_2016}.

\subsection{Coordinate Definitions}
The Roborodentia field is 2438.4 mm long in the $x$ direction and 1219.2 mm wide in $y$ as shown in Figure \ref{fig:field_defs} \cite{roborodentia}. Viewed from above, the coordinate (0 mm, 0 mm) is the bottom-left corner while (2438.4 mm, 1219.2 mm) is the top-right. Units of position ($x$ and $y$), orientation, linear velocity, and rotational velocity are mm, mm/s, radians, and radians/s, respectively.

The robot position and orientation, ($x$, $y$, $\theta$), is represented as a vector in the field plane where the vector's tail is positioned at the robot center and tip at the robot's front. Note that the vector orientation deviates from standard notation. At 0 radians, the vector points in the $+y$ direction, and at $+\pi/2$ radians, it points towards $-x$. 

The $x$ and $y$ velocity of the robot refer to motion parallel to the field's x-axis and y-axis while the rotational velocity refers to the robot's rotation about its center. They are defined as $\dot{x}$, $\dot{y}$, and $\dot{\theta}$. 

Three control inputs $u_x$, $u_y$, and $u_\theta$ correspond to the force applied to the robot and range between -2 to +2. For absolute clarity, positive $u_x$ moves the robot in the direction of the positive x-axis, positive $u_y$ pushes towards the positive y-axis, and positive $u_\theta$ torques the robot in the positive $\theta$ direction. 
\begin{figure}[H]
	
	\caption{Roborodentia Field Definitions} \label{fig:field_defs}
\end{figure}

\subsection{Robot Simulation}
Since training the network using the real-life robot is difficult and time-consuming, episodes take place in a simulation of the robot and competition field. While an ideal simulation would model many kinematics and dynamics of the robot, robust system modeling is beyond the scope of the thesis. Instead, a rudimentary model serves to demonstrate the efficacy of the DDPG algorithm. 

The simulation accounts for maximum wheel velocity and acceleration and calculates robot movement as a function of the four wheel velocities using the mecanum wheel equations \cite{li_2018}\cite{rahman_2014}. It also handles collision with the environment walls. The simulation does not model unequal loading and friction between wheels, the momentum of the robot as a whole, or small differences between the motors and wheels.

\subsection{Reward Assignment}
The reward assignment must reflect the actor's goal: to move the robot to a desired position and orientation in the field. The resulting policy after training depends greatly on careful selection of which actions and/or states receive better or worse rewards. The rewards as implemented, shown in Equations \ref{eq:reward_x} to \ref{eq:reward_uth}, consist of three categories: distance from the set point, velocity, and action value. Note that the $\text{norm}(\cdot)$ function normalizes the angle to between $-\pi$ and $+\pi$. Each of the nine reward equations produces a maximum reward of 0 and includes squared terms to introduce quadratic reward scaling.

The coefficients for $r_\theta$, $r_{\dot{\theta}}$, and $r_{u_\theta}$ come from OpenAI Gym's pendulum environment \cite{openai_pendulum}. The other coefficients scale the reward magnitudes within each category close to each other. For example, the minimum $r_{y} = -0.00001 (1200 - 0)^2 = -14.4$ while the minimum $r_{\theta} = -1.0 (\pi)^2 = -9.9$. Finally, the coefficients were adjusted through trial-and-error: the algorithm was run multiple times with slightly varied coefficients until the author felt the policy was ``good enough''. Future work includes a more systematic way to determine these coefficients.
\begin{align}
r_x &= -0.00001 (x-x_{desired})^2 \label{eq:reward_x}\\
r_y &= -0.00001 (y-y_{desired})^2 \\
r_\theta &= -1.0 (norm(\theta)-norm(\theta_{desired}))^2 \\
r_{\dot{x}} &= -0.0000005 \dot{x}^2 \\
r_{\dot{y}} &= -0.0000005 \dot{y}^2 \\
r_{\dot{\theta}} &= -0.1 \dot{\theta}^2 \\
r_{u_x} &= -0.001u_x^2 \\
r_{u_y} &= -0.001u_y^2 \\
r_{u_\theta} &= -0.001u_\theta^2 \label{eq:reward_uth}
\end{align}
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

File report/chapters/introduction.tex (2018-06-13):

\chapter{Introduction}
The game of Go has challenged players around the world for centuries, and since the 1970's, international competitions have sought the world's best Go minds \cite{go}. The relatively simple rules of the game betray its true complexity and myriad moves; for example, there are 361 possible opening moves while chess has a mere 20 \cite{brit_go}. In fact, for the 19x19 Go board, about $\num{2e170}$ possible board states exist which is about $10^{90}$ times more than the number of atoms in the known universe \cite{go_num}. To produce a Go-playing artificial intelligence (AI) at the level of a human expert has been somewhat of a holy grail for machine learning researchers \cite{brit_go2}. Until 2014, the very best Go programs were only capable of occasionally beating top amateur players. However, in 2015, AlphaGo grabbed the world's attention with a landmark win, beating European champion Go player Fan Hui in a 5--0 upset \cite{brit_go3}. In March 2016, AlphaGo defeated 18-time world champion Lee Sedol 4--1. The success of AlphaGo's policy gradient-based algorithms along with the development of the deep deterministic policy gradient (DDPG) method from DeepMind paved the way for improvements in reinforcement learning, especially in the previously intractable area of continuous control \cite{Mnih_2015}\cite{silver_2017}.
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

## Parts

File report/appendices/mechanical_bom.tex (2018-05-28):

\chapter{Mechanical Parts -- Bill of Materials}
\label{appendix:mech_bom}

\LTXtable{\textwidth}{tables/tab_mech_bom.tex}

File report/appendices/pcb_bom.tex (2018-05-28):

\chapter{Interconnect PCB Bill of Materials}
\label{appendix:pcb_bom}

\begin{landscape}
\small
\LTXtable{600pt}{tables/tab_pcb_bom.tex}
\end{landscape}

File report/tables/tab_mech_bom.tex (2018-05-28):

\begin{longtable}{clr}
	\caption{Mechanical Bill of Materials}	\label{tab:mech_bom}\\
	\toprule
	ITEM NO. & \multicolumn{1}{c}{PART FILE NAME}      & \multicolumn{1}{c}{QTY.} \\ 
	\midrule
	\endfirsthead
	
	\toprule
	ITEM NO. & \multicolumn{1}{c}{PART FILE NAME}      & \multicolumn{1}{c}{QTY.} \\ 
	\midrule
	\endhead

	1.        & battery                                 & 1                        \\ 
	2.        & battery\_mount                          & 1                        \\ 
	3.        & blower                                  & 1                        \\ 
	4.        & bottom\_plate                           & 1                        \\ 
	5.        & buck\_converter                         & 2                        \\ 
	6.        & button                                  & 1                        \\ 
	7.        & button\_mount                           & 1                        \\ 
	8.        & control\_brd                            & 1                        \\ 
	9.        & dual\_flywheel\_cage\_fixed             & 1                        \\ 
	10.       & electrical\_mount                       & 1                        \\ 
	11.       & electrical\_mount\_bracket\_angled      & 2                        \\ 
	12.       & hopper\_bar                             & 2                        \\ 
	13.       & hopper\_connector                       & 2                        \\ 
	14.       & imu                                     & 1                        \\ 
	15.       & launcher\_motor\_small                  & 2                        \\ 
	16.       & m2-12                                   & 2                        \\ 
	17.       & m2-8                                    & 12                       \\ 
	18.       & m2-nut                                  & 14                       \\ 
	19.       & m3-12                                   & 86                       \\ 
	20.       & m3-20                                   & 2                        \\ 
	21.       & m3-25                                   & 4                        \\ 
	22.       & m3-30                                   & 16                       \\ 
	23.       & m3-35                                   & 4                        \\ 
	24.       & m3-40                                   & 5                        \\ 
	25.       & m3-45                                   & 12                       \\ 
	26.       & m3-nut                                  & 115                      \\ 
	27.       & m3-standoff-5                           & 4                        \\ 
	28.       & m4-12                                   & 8                        \\ 
	29.       & m4-nut                                  & 8                        \\ 
	30.       & mecanum\_coupler                        & 4                        \\ 
	31.       & mecanum\_wheel                          & 4                        \\ 
	32.       & motor\_clamp                            & 2                        \\ 
	33.       & motor\_driver                           & 3                        \\ 
	34.       & NUCLEO\_F446RE                          & 1                        \\ 
	35.       & nylon\_standoff                         & 36                       \\ 
	36.       & pusher\_mount                           & 1                        \\ 
	37.       & rangefinder                             & 4                        \\ 
	38.       & rangefinder\_mount                      & 4                        \\ 
	39.       & Raspberry Pi 3 Light Version            & 1                        \\ 
	40.       & servo                                   & 1                        \\ 
	41.       & servo\_hopper                           & 1                        \\ 
	42.       & servo\_hopper\_gate                     & 1                        \\ 
	43.       & servo\_hopper\_mount\_base\_mini        & 1                        \\ 
	44.       & servo\_hopper\_mount\_base\_right\_mini & 1                        \\ 
	45.       & servo\_hopper\_mount\_bracket           & 2                        \\ 
	46.       & servo\_hopper\_servo\_mount             & 1                        \\ 
	47.       & servo\_horn                             & 1                        \\ 
	48.       & switch                                  & 1                        \\ 
	49.       & switch\_mount                           & 1                        \\ 
	50.       & venturi\_loader\_fixed                  & 1                        \\ 
	51.       & wheel\_grip\_small                      & 2                        \\ 
	52.       & wheel\_motor                            & 4                        \\ 
	53.       & wheel\_motor\_bracket                   & 4                        \\ 
			 & TOTAL                                   & 394                      \\ 
	\bottomrule
\end{longtable}

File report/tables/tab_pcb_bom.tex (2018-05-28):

\begin{longtable}{rrp{3in}p{1.5in}p{1.7in}}
	\caption{Interconnect PCB Bill of Materials} \label{tab:pcb_bom} \\
	\toprule
	\multicolumn{1}{c}{Qty} & \multicolumn{1}{c}{Value} & \multicolumn{1}{c}{Parts} & \multicolumn{1}{c}{Description} & \multicolumn{1}{c}{DIGIKEY PN} \\ 
	\midrule
	\endfirsthead
	\toprule
	\multicolumn{1}{c}{Qty} & \multicolumn{1}{c}{Value} & \multicolumn{1}{c}{Parts} & \multicolumn{1}{c}{Description} & \multicolumn{1}{c}{DIGIKEY PN} \\ 
	\midrule
	\endhead
	
	2 & AZ1085CD & U2, U7 & AZ1085C & AZ1085CD-ADJTRG1DICT-ND \\ 
	7 & 0.1uF & C3, C4, C5, C6, C7, C8, C9 & CAPACITOR & 445-5667-1-ND \\ 
	2 & 10uF3 & C1, C2 & CAPACITOR & 490-13248-1-NDÊ \\ 
	2 & 22uF & C10, C11 & CAPACITOR & 490-10476-1-ND \\ 
	3 & TCA9554A & U1, U5, U6 & I2C GPIO Expander & 296-45456-1-ND \\ 
	6 &  & X1, X12, X16, X18, X19, X20 & JST XH 2 Pin & 455-2247-ND \\ 
	2 &  & X13, X14 & JST XH 3 Pin & 455-2248-ND \\ 
	1 &  & X8 & JST XH 4 Pin & 455-2249-ND \\ 
	6 &  & X2, X3, X4, X5, X6, X7 & JST XH 6 Pin & 455-2271-ND \\ 
	3 &  & X9, X10, X11 & JST XH 7 Pin & 455-2252-ND \\ 
	2 &  & X15, X17 & JST XH 8 Pin & 455-2251-ND \\ 
	6 & GREEN & LED1, LED2, LED3, LED4, LED5, LED6 & LED & 732-4971-1-ND \\ 
	2 & RE1C002UN & Q1, Q2 & Logic-level N-FET & RE1C002UNTCLCT-ND \\ 
	4 & 82 & R7, R9, R10, R18 & RESISTOR & 311-82.0HRCT-ND \\ 
	5 & 100 & R3, R11, R12, R15, R16 & RESISTOR & 311-100HRCT-ND \\ 
	1 & 178 & R1 & RESISTOR & 311-178HRCT-ND \\ 
	1 & 287 & R2 & RESISTOR & 311-287HRCT-ND \\ 
	1 & 301 & R4 & RESISTOR & 311-301HRCT-ND \\ 
	2 & 430 & R8, R17 & RESISTOR & 311-430HRCT-ND \\ 
	4 & 3.3k & R19, R20, R21, R22 & RESISTOR & 311-3.30KHRCT-ND \\ 
	4 & 4.7k & R5, R6, R13, R14 & RESISTOR & 311-4.70KHRCT-ND \\ 
	2 & SPST & SW1, SW2 & SMT 6mm switch & P12955SCT-ND \\ 
	1 & STM32F446 & U4 & NUCLEO-64 & 497-15882-ND \\ 
	10 & & PAD1, PAD2, PAD3, PAD4, PAD5, PAD6, PAD7, PAD8, PAD9, PAD10 & Wire Pad & n/a \\ 
	105 & & SB1, SB2, SB3, SB4, SB5, SB6, SB7, SB8, SB9, SB10, SB11, SB12, SB13, SB14, SB15, SB16, SB17, SB18, SB19, SB20, SB21, SB22, SB23, SB24, SB25, SB26, SB27, SB28, SB29, SB30, SB31, SB32, SB33, SB34, SB35, SB36, SB37, SB38, SB39, SB40, SB41, SB42, SB43, SB44, SB45, SB46, SB47, SB48, SB49, SB50, SB51, SB52, SB54, SB55, SB56, SB57, SB58, SB59, SB60, SB61, SB62, SB63, SB64, SB65, SB66, SB67, SB68, SB69, SB70, SB71, SB72, SB73, SB75, SB76, SB77, SB78, SB80, SB81, SB82, SB83, SB94, SB96, SB98, SB99, SB100, SB101, SB102, SB103, SB104, SB105, SB106, SB107, SB108, SB109, SB110, SB111, SB112, SB113, SB114, SB115, SB116, SB117, SB118, SB119, SB120 & Solder bridge with knife-cuttable prebridged connection. & n/a \\ 
	\bottomrule
\end{longtable}

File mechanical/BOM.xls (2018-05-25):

ITEM NO. | PART FILE NAME | QTY.
1 | battery | 1
2 | battery_mount | 1
3 | blower | 1
4 | bottom_plate | 1
5 | buck_converter | 2
6 | button | 1
7 | button_mount | 1
8 | control_brd | 1
9 | dual_flywheel_cage_fixed | 1
10 | electrical_mount | 1
11 | electrical_mount_bracket_angled | 2
12 | hopper_bar | 2
13 | hopper_connector | 2
14 | imu | 1
15 | launcher_motor_small | 2
16 | m2-12 | 2
17 | m2-8 | 12
18 | m2-nut | 14
19 | m3-12 | 86
20 | m3-20 | 2
21 | m3-25 | 4
22 | m3-30 | 16
23 | m3-35 | 4
24 | m3-40 | 5
25 | m3-45 | 12
26 | m3-nut | 115
27 | m3-standoff-5 | 4
28 | m4-12 | 8
29 | m4-nut | 8
30 | mecanum_coupler | 4
31 | mecanum_wheel | 4
32 | motor_clamp | 2
33 | motor_driver | 3
34 | NUCLEO_F446RE | 1
35 | nylon_standoff | 36
36 | pusher_mount | 1
37 | rangefinder | 4
38 | rangefinder_mount | 4
39 | Raspberry Pi 3 Light Version | 1
40 | servo | 1
41 | servo_hopper | 1
42 | servo_hopper_gate | 1
43 | servo_hopper_mount_base_mini | 1
44 | servo_hopper_mount_base_right_mini | 1
45 | servo_hopper_mount_bracket | 2
46 | servo_hopper_servo_mount | 1
47 | servo_horn | 1
48 | switch | 1
49 | switch_mount | 1
50 | venturi_loader_fixed | 1
51 | wheel_grip_small | 2
52 | wheel_motor | 4
53 | wheel_motor_bracket | 4
 | TOTAL | 394

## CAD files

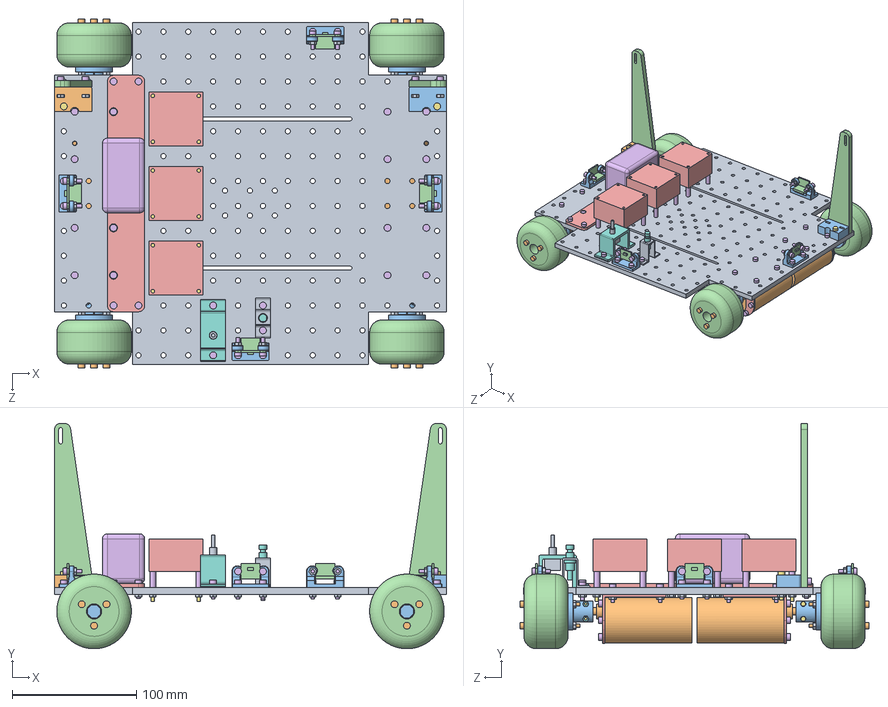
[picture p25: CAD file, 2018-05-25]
mechanical/assems/base_platform.SLDASM
315.0 x 181.2 x 280.2 mm
bottom_plate
wheel_motor x 4
mecanum_coupler x 4
mecanum_wheel x 4
wheel_motor_bracket x 4
m3-12 x 68
m2-8 x 8
m2-nut x 8
m3-nut x 72
m3-45 x 12
rangefinder_mount x 4
rangefinder x 4
motor_driver x 3
nylon spacer x 12
m3-30 x 12
switch_mount
switch
servo_hopper_mount_base_mini
servo_hopper_mount_base_right_mini
servo_hopper_mount_bracket x 2
battery_mount
battery
m3-20 x 2
button
button_mount

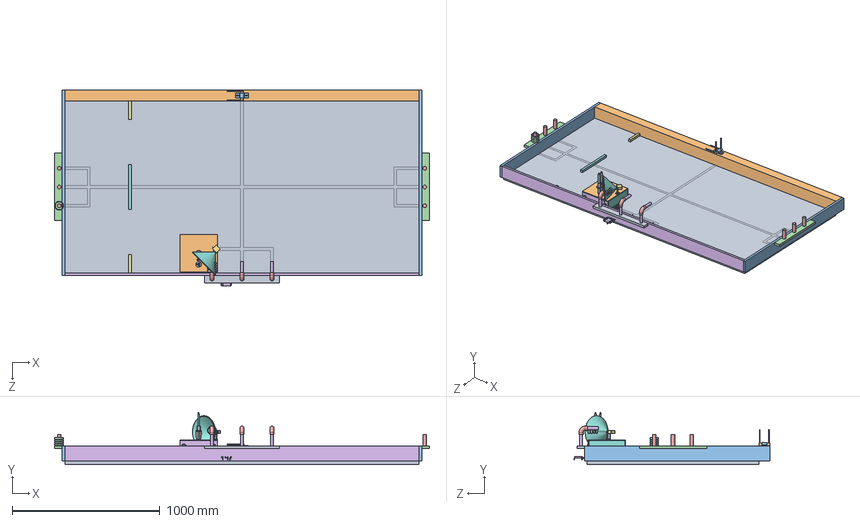
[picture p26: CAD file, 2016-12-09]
mechanical/field/field.SLDASM
2540.0 x 352.8 x 1328.2 mm
field_floor
field_centerwall
field_shortwall x 2
field_sidepegholder x 2
field_scoringpeg x 6
field_longwall
field_shortbump x 2
field_longbump
field_frontpegholder
field_flag
field_flagbracket
ring x 8
field_supplypeg_elbow x 3
field_supplypeg_straight x 6
base_board
wheel_motor_bracket x 4
wheel_motor x 4
Omniwheelcoupling[1] x 4
Omniwheelcoupling[2] x 4
TheRealOmniWheel x 4
loller x 64
NUCLEO_F446RE
nylon spacer x 3
acme_screw
acme_screw_nut
0.25_pulley
0.125_pulley
arcade_button x 2
dc_motor_shaft
chassis_front
chassis_rear
chassis_left
chassis_right
chassis_top
nylon_bearing
linear_bearing
linear_shaft
6383K213_BALL BEARING
servo
servo_horn
servo_mount_temp

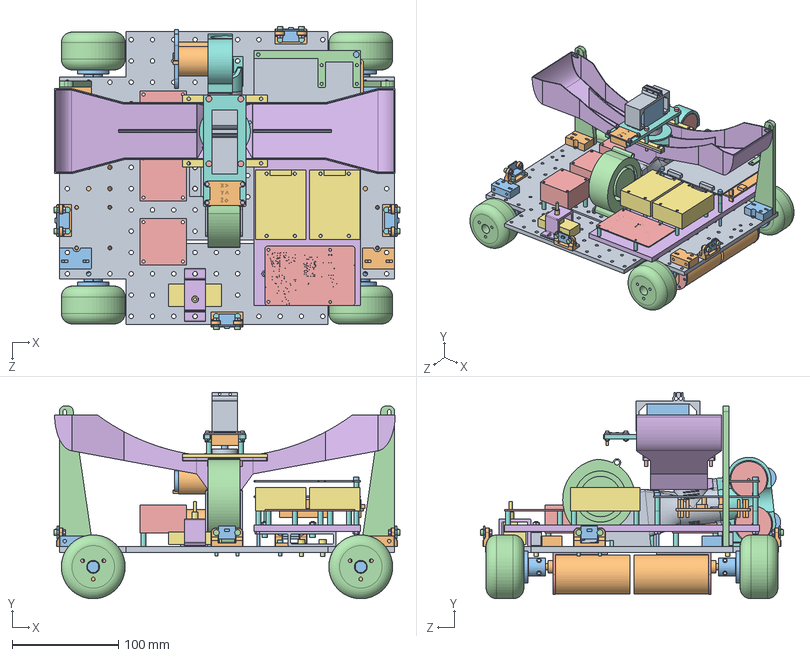
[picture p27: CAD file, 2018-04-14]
mechanical/robot_assem.SLDASM
325.1 x 194.0 x 285.1 mm
bottom_plate
wheel_motor x 4
mecanum_coupler x 4
mecanum_wheel x 4
wheel_motor_bracket x 4
electrical_mount
buck_converter x 2
nylon spacer x 37
control_brd
NUCLEO_F446RE
m3-50 x 4
imu_mount_small
Raspberry Pi 3 Light Version
m3-nut x 22
m4-12 x 4
m3-12 x 12
electrical_mount_bracket_angled x 2
rangefinder_mount x 4
rangefinder x 4
m3-8 x 14
motor_driver x 3
switch_mount
switch
dual_flywheel_cage_fixed
venturi_loader_fixed
launcher_motor_small x 2
motor_clamp x 2
blower
wheel_grip_small x 2
servo_hopper - Copy
hopper_connector x 2
servo_hopper_servo_mount
servo_horn
imu
servo
m3-standoff-5 x 4
m3-30 x 4
m2-8 x 4
m2-nut x 4
servo_hopper_gate2
pusher_mount
servo_hopper_mount_base_mini x 2
servo_hopper_mount_base_right_mini x 2
servo_hopper_mount_bracket x 2

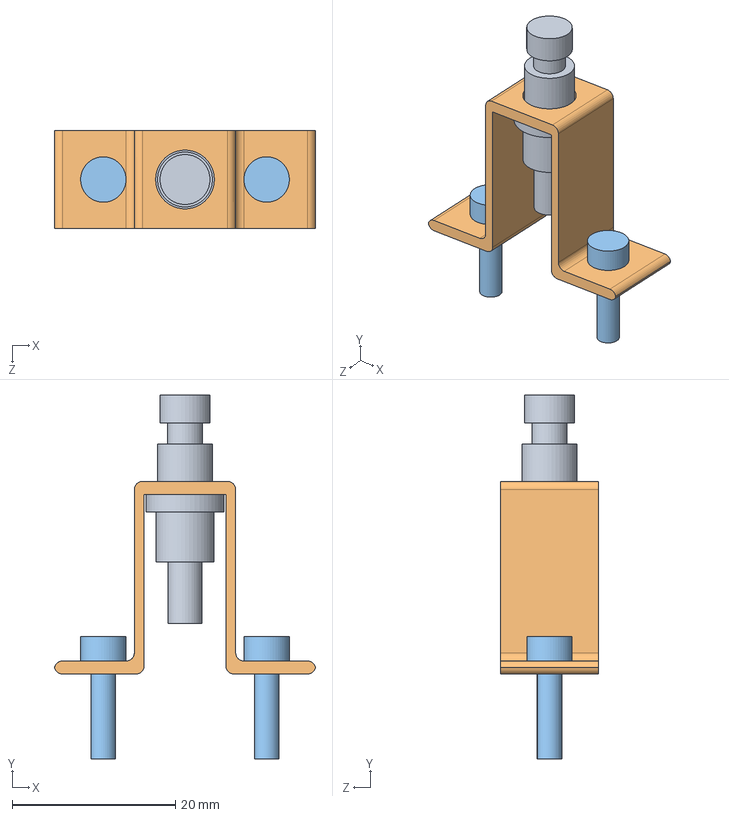
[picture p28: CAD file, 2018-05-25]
mechanical/assems/button_mounted.SLDASM
32.0 x 44.6 x 12.0 mm
button
button_mount
m3-12 x 2

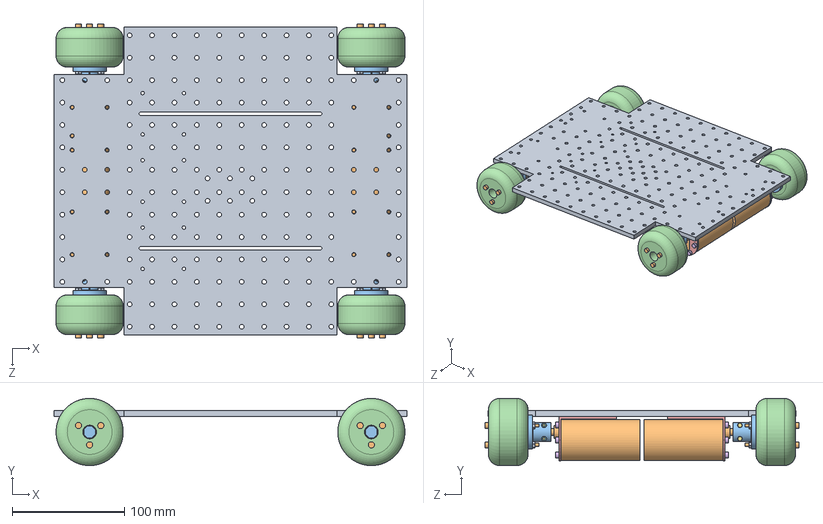
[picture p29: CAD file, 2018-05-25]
mechanical/assems/robot_base.SLDASM
315.0 x 60.0 x 280.2 mm
bottom_plate
wheel_motor x 4
mecanum_coupler x 4
mecanum_wheel x 4
wheel_motor_bracket x 4
m3-12 x 24
m2-8 x 8
m2-nut x 8
m3-nut x 12
m3-45 x 12

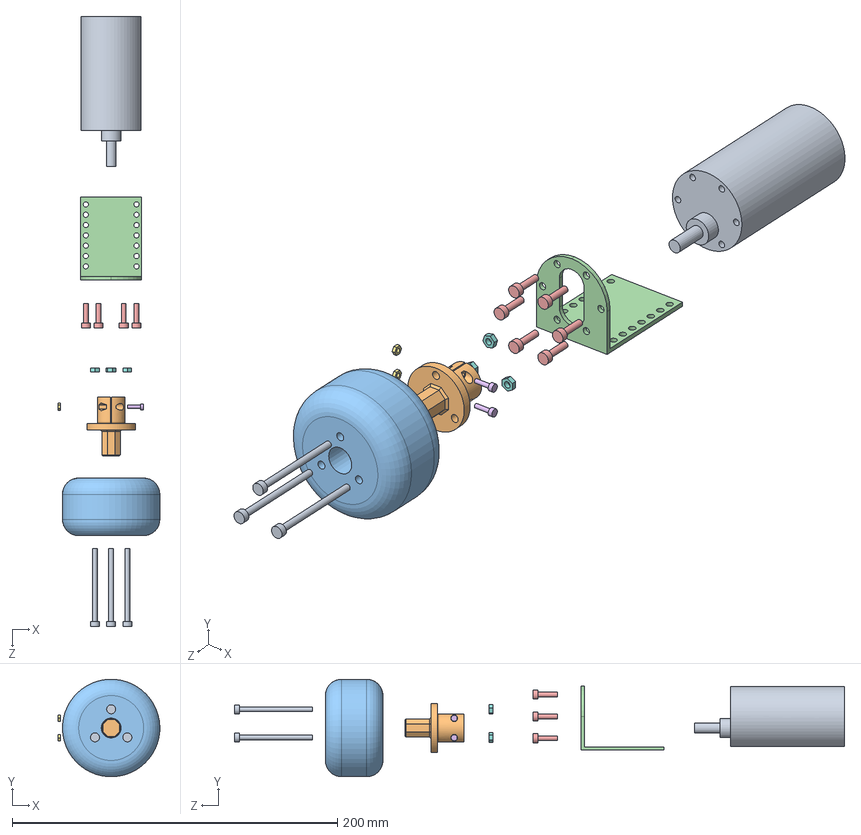
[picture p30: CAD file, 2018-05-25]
mechanical/assems/drive_motor_assem.SLDASM
62.6 x 60.0 x 375.4 mm
wheel_motor
mecanum_coupler
mecanum_wheel
wheel_motor_bracket
m3-12 x 6
m2-8 x 2
m2-nut x 2
m3-nut x 3
m3-45 x 3

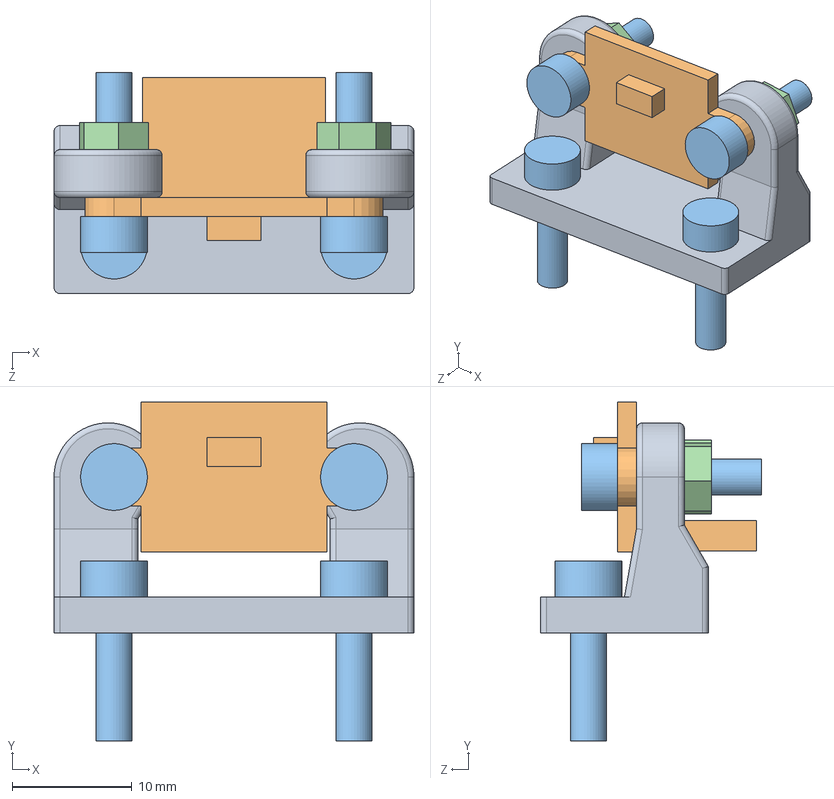
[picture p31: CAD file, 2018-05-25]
mechanical/assems/rangefinder_mounted.SLDASM
30.0 x 28.2 x 18.4 mm
rangefinder_mount
rangefinder
m3-12 x 4
m3-nut x 2

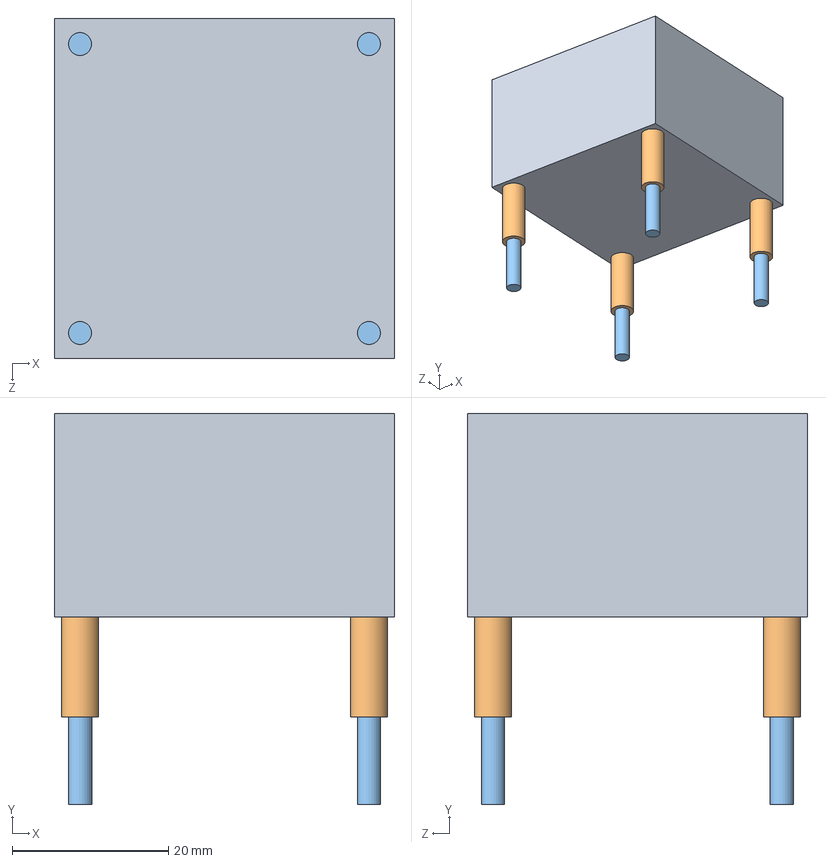
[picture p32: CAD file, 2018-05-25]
mechanical/assems/motor_driver_standoff.SLDASM
43.5 x 50.0 x 43.5 mm
motor_driver
nylon spacer x 4
m3-30 x 4

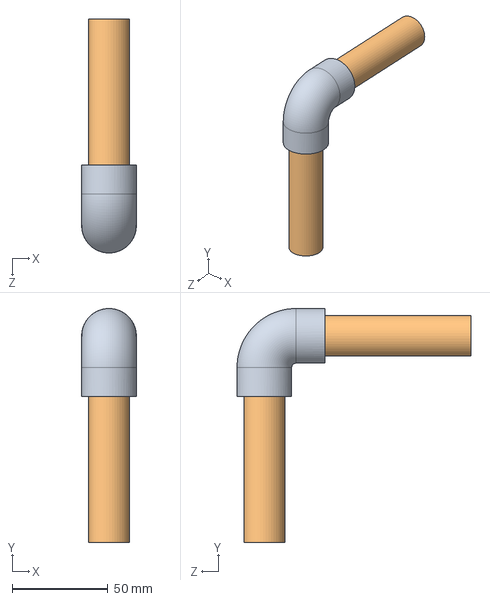
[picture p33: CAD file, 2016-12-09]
mechanical/field/field_supplypeg.SLDASM
28.6 x 122.2 x 122.2 mm
field_supplypeg_elbow
field_supplypeg_straight x 2

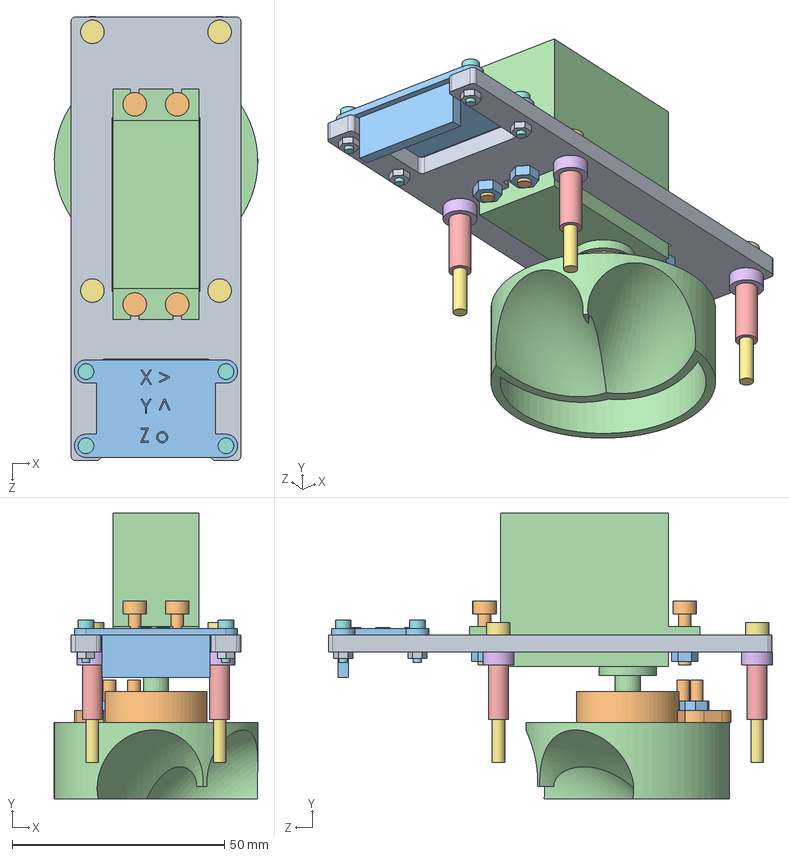
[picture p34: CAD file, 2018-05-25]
mechanical/assems/hopper_servo_mount.SLDASM
48.0 x 67.4 x 104.8 mm
servo_hopper_servo_mount
servo_horn
imu
servo
nylon spacer x 4
m3-standoff-5 x 4
m3-30 x 4
m2-8 x 4
m2-nut x 4
m3-12 x 6
m3-nut x 6
servo_hopper_gate

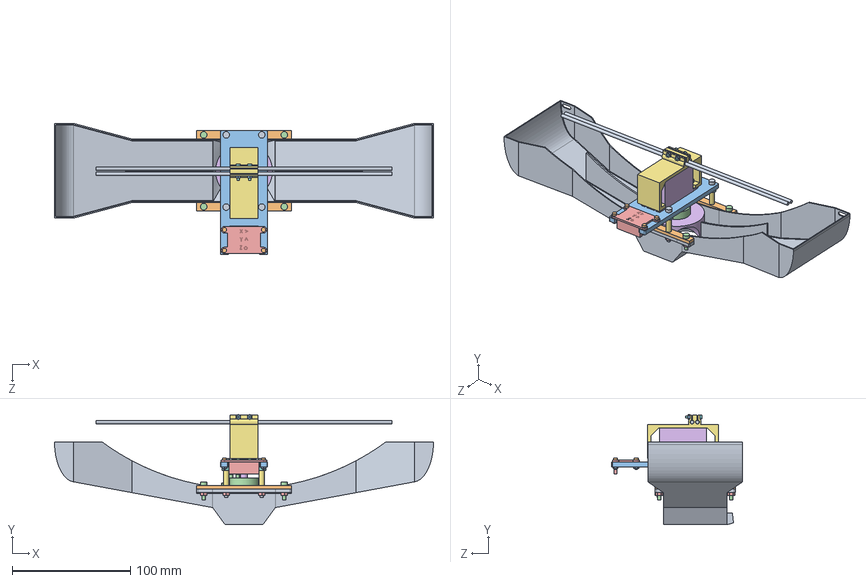
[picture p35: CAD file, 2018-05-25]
mechanical/assems/hopper_fixed.SLDASM
320.0 x 93.1 x 110.8 mm
servo_hopper - Copy
hopper_connector x 2
servo_hopper_servo_mount
servo_horn
imu
servo
nylon spacer x 4
m3-standoff-5 x 4
m3-30 x 4
m2-8 x 4
m2-nut x 6
m3-12 x 10
m3-nut x 14
servo_hopper_gate
pusher_mount
m2-12 x 2
hopper_bar x 2

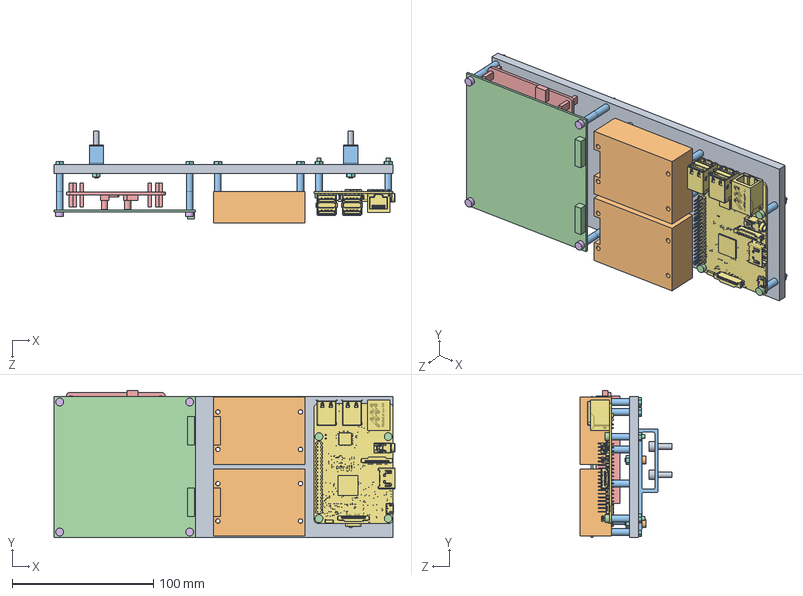
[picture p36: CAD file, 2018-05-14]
mechanical/assems/electrical_mount_assem.SLDASM
241.3 x 104.3 x 64.8 mm
electrical_mount
buck_converter x 2
nylon spacer x 20
control_brd
NUCLEO_F446RE
m3-35 x 4
Raspberry Pi 3 Light Version
m3-nut x 20
m4-12 x 4
m3-12 x 4
electrical_mount_bracket_angled x 2
m3-25 x 4

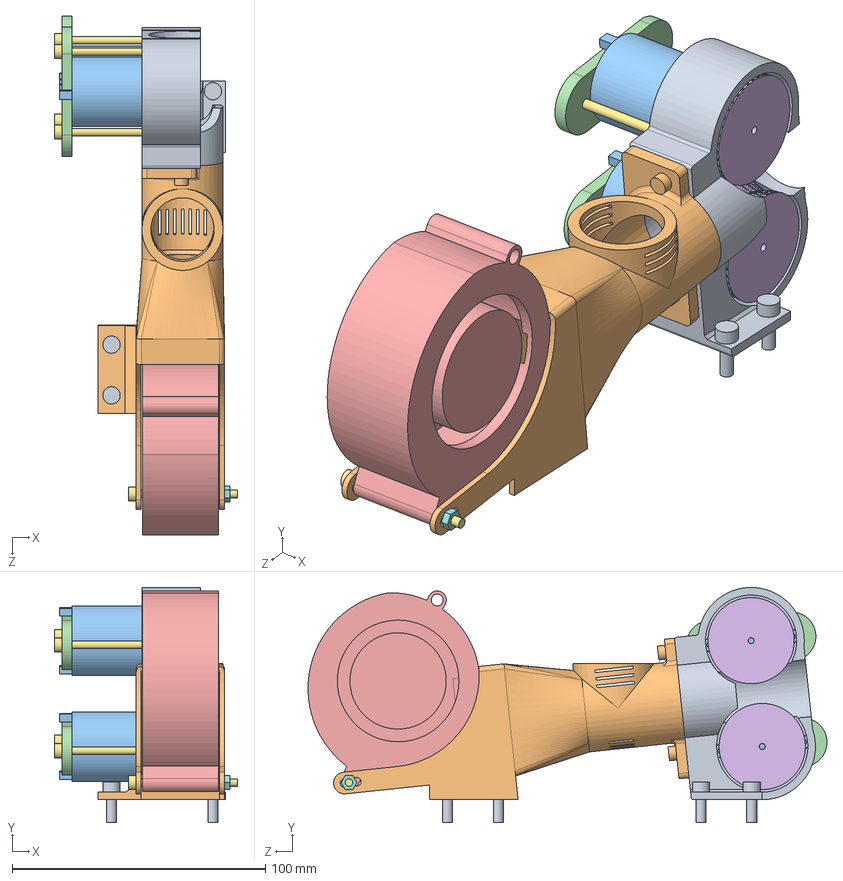
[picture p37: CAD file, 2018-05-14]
mechanical/assems/dual_flywheel_cage_fixed.SLDASM
72.3 x 92.8 x 204.8 mm
dual_flywheel_cage_fixed
venturi_loader_fixed
launcher_motor_small x 2
motor_clamp x 2
blower
wheel_grip_small x 2
m3-40 x 5
m3-nut x 7
m4-12 x 4
m3-12 x 2

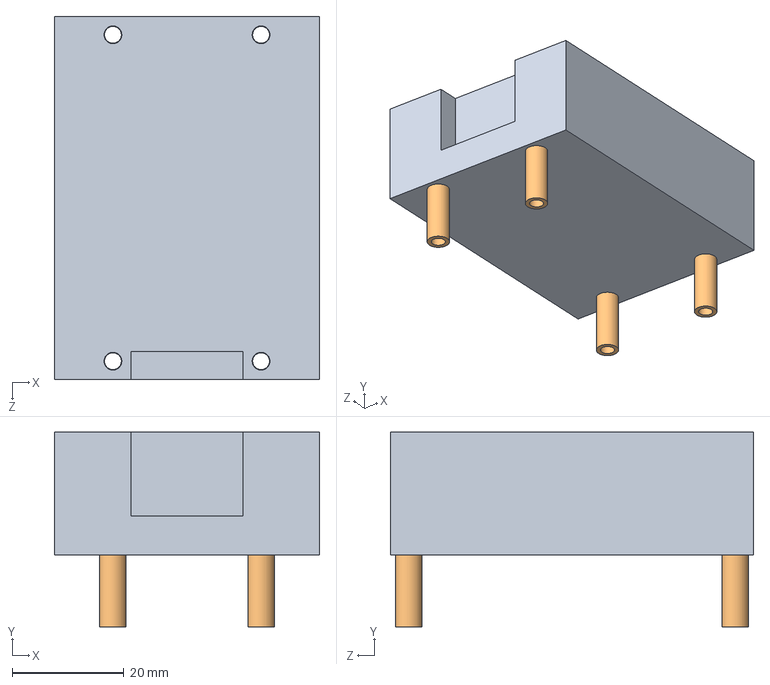
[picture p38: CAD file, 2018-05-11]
mechanical/assems/buck_converter_standoff.SLDASM
47.5 x 34.8 x 65.0 mm
buck_converter
nylon spacer x 4

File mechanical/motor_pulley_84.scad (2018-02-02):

// Parametric Pulley with multiple belt profiles
// by droftarts January 2012

// Based on pulleys by:
// http://www.thingiverse.com/thing:11256 by me!
// https://github.com/prusajr/PrusaMendel by Josef Prusa
// http://www.thingiverse.com/thing:3104 by GilesBathgate
// http://www.thingiverse.com/thing:2079 by nophead

// dxf tooth data from http://oem.cadregister.com/asp/PPOW_Entry.asp?company=915217&elementID=07807803/METRIC/URETH/WV0025/F
// pulley diameter checked and modelled from data at http://www.sdp-si.com/D265/HTML/D265T016.html

/**
 * @name Pulley
 * @category Printed
 * @using 1 x m3 nut, normal or nyloc
 * @using 1 x m3x10 set screw or 1 x m3x8 grub screw
 */


// tuneable constants

teeth = 84;			// Number of teeth, standard Mendel T5 belt = 8, gives Outside Diameter of 11.88mm
profile = 12;		// 1=MXL 2=40DP 3=XL 4=H 5=T2.5 6=T5 7=T10 8=AT5 9=HTD_3mm 10=HTD_5mm 11=HTD_8mm 12=GT2_2mm 13=GT2_3mm 14=GT2_5mm

motor_shaft = 3.5;	// NEMA17 motor shaft exact diameter = 5
m3_dia = 3.3;		// 3mm hole diameter
m3_nut_hex = 1;		// 1 for hex, 0 for square nut
m3_nut_flats = 5.7;	// normal M3 hex nut exact width = 5.5
m3_nut_depth = 2.7;	// normal M3 hex nut exact depth = 2.4, nyloc = 4

retainer = 1;		// Belt retainer above teeth, 0 = No, 1 = Yes
retainer_ht = 1.5;	// height of retainer flange over pulley, standard = 1.5
idler = 1;			// Belt retainer below teeth, 0 = No, 1 = Yes
idler_ht = 1.5;		// height of idler flange over pulley, standard = 1.5

pulley_t_ht = 6.2;	// length of toothed part of pulley, standard = 12
pulley_b_ht = 8;		// pulley base height, standard = 8. Set to same as idler_ht if you want an idler but no pulley.
pulley_b_dia = 20;	// pulley base diameter, standard = 20
no_of_nuts = 1;		// number of captive nuts required, standard = 1
nut_angle = 90;		// angle between nuts, standard = 90
nut_shaft_distance = 1.2;	// distance between inner face of nut and shaft, can be negative.


//	********************************
//	** Scaling tooth for good fit **
//	********************************
/*	To improve fit of belt to pulley, set the following constant. Decrease or increase by 0.1mm at a time. We are modelling the *BELT* tooth here, not the tooth on the pulley. Increasing the number will *decrease* the pulley tooth size. Increasing the tooth width will also scale proportionately the tooth depth, to maintain the shape of the tooth, and increase how far into the pulley the tooth is indented. Can be negative */

additional_tooth_width = -0.2; //mm

//	If you need more tooth depth than this provides, adjust the following constant. However, this will cause the shape of the tooth to change.

additional_tooth_depth = 0.4; //mm

// calculated constants

nut_elevation = pulley_b_ht/2;
m3_nut_points = 2*((m3_nut_flats/2)/cos(30)); // This is needed for the nut trap

// The following set the pulley diameter for a given number of teeth

MXL_pulley_dia = tooth_spacing (2.032,0.254);
40DP_pulley_dia = tooth_spacing (2.07264,0.1778);
XL_pulley_dia = tooth_spacing (5.08,0.254);
H_pulley_dia = tooth_spacing (9.525,0.381);
T2_5_pulley_dia = tooth_spaceing_curvefit (0.7467,0.796,1.026);
T5_pulley_dia = tooth_spaceing_curvefit (0.6523,1.591,1.064);
T10_pulley_dia = tooth_spacing (10,0.93);
AT5_pulley_dia = tooth_spaceing_curvefit (0.6523,1.591,1.064);
HTD_3mm_pulley_dia = tooth_spacing (3,0.381);
HTD_5mm_pulley_dia = tooth_spacing (5,0.5715);
HTD_8mm_pulley_dia = tooth_spacing (8,0.6858);
GT2_2mm_pulley_dia = tooth_spacing (2,0.254);
GT2_3mm_pulley_dia = tooth_spacing (3,0.381);
GT2_5mm_pulley_dia = tooth_spacing (5,0.5715);

// The following calls the pulley creation part, and passes the pulley diameter and tooth width to that module

if ( profile == 1 ) { pulley ( "MXL" , MXL_pulley_dia , 0.508 , 1.321 ); }
if ( profile == 2 ) { pulley ( "40 D.P." , 40DP_pulley_dia , 0.457 , 1.226 ); }
if ( profile == 3 ) { pulley ( "XL" , XL_pulley_dia , 1.27, 3.051 ); }
if ( profile == 4 ) { pulley ( "H" , H_pulley_dia ,1.905 , 5.359 ); }
if ( profile == 5 ) { pulley ( "T2.5" , T2_5_pulley_dia , 0.7 , 1.678 ); }
if ( profile == 6 ) { pulley ( "T5" , T5_pulley_dia , 1.19 , 3.264 ); }
if ( profile == 7 ) { pulley ( "T10" , T10_pulley_dia , 2.5 , 6.13 ); }
if ( profile == 8 ) { pulley ( "AT5" , AT5_pulley_dia , 1.19 , 4.268 ); }
if ( profile == 9 ) { pulley ( "HTD 3mm" , HTD_3mm_pulley_dia , 1.289 , 2.27 ); }
if ( profile == 10 ) { pulley ( "HTD 5mm" , HTD_5mm_pulley_dia , 2.199 , 3.781 ); }
if ( profile == 11 ) { pulley ( "HTD 8mm" , HTD_8mm_pulley_dia , 3.607 , 6.603 ); }
if ( profile == 12 ) { pulley ( "GT2 2mm" , GT2_2mm_pulley_dia , 0.764 , 1.494 ); }
if ( profile == 13 ) { pulley ( "GT2 3mm" , GT2_3mm_pulley_dia , 1.169 , 2.31 ); }
if ( profile == 14 ) { pulley ( "GT2 5mm" , GT2_5mm_pulley_dia , 1.969 , 3.952 ); }

// Functions

function tooth_spaceing_curvefit (b,c,d)
	= ((c * pow(teeth,d)) / (b + pow(teeth,d))) * teeth ;

function tooth_spacing(tooth_pitch,pitch_line_offset)
	= (2*((teeth*tooth_pitch)/(3.14159265*2)-pitch_line_offset)) ;

// Main Module

module pulley( belt_type , pulley_OD , tooth_depth , tooth_width )
	{
	echo (str("Belt type = ",belt_type,"; Number of teeth = ",teeth,"; Pulley Outside Diameter = ",pulley_OD,"mm "));
	tooth_distance_from_centre = sqrt( pow(pulley_OD/2,2) - pow((tooth_width+additional_tooth_width)/2,2));
	tooth_width_scale = (tooth_width + additional_tooth_width ) / tooth_width;
	tooth_depth_scale = ((tooth_depth + additional_tooth_depth ) / tooth_depth) ;


//	************************************************************************
//	*** uncomment the following line if pulley is wider than puller base ***
//	************************************************************************

//	translate ([0,0, pulley_b_ht + pulley_t_ht + retainer_ht ]) rotate ([0,180,0])

	difference()
	 {	 
		union()
		{
			//base
	
			if ( pulley_b_ht < 2 ) { echo ("CAN'T DRAW PULLEY BASE, HEIGHT LESS THAN 2!!!"); } else {
				rotate_extrude($fn=pulley_b_dia*2)
				{
						square([pulley_b_dia/2-1,pulley_b_ht]);
						square([pulley_b_dia/2,pulley_b_ht-1]);
						translate([pulley_b_dia/2-1,pulley_b_ht-1]) circle(1);
				}
			}
	
		difference()
			{
			//shaft - diameter is outside diameter of pulley
			
			translate([0,0,pulley_b_ht]) 
			rotate ([0,0,360/(teeth*4)]) 
			cylinder(r=pulley_OD/2,h=pulley_t_ht, $fn=teeth*4);
	
			//teeth - cut out of shaft
		
			for(i=[1:teeth]) 
			rotate([0,0,i*(360/teeth)])
			translate([0,-tooth_distance_from_centre,pulley_b_ht -1]) 
			scale ([ tooth_width_scale , tooth_depth_scale , 1 ]) 
			{
			if ( profile == 1 ) { MXL();}
			if ( profile == 2 ) { 40DP();}
			if ( profile == 3 ) { XL();}
			if ( profile == 4 ) { H();}
			if ( profile == 5 ) { T2_5();}
			if ( profile == 6 ) { T5();}
			if ( profile == 7 ) { T10();}
			if ( profile == 8 ) { AT5();}
			if ( profile == 9 ) { HTD_3mm();}
			if ( profile == 10 ) { HTD_5mm();}
			if ( profile == 11 ) { HTD_8mm();}
			if ( profile == 12 ) { GT2_2mm();}
			if ( profile == 13 ) { GT2_3mm();}
			if ( profile == 14 ) { GT2_5mm();}
			}

			}
			
		//belt retainer / idler
		if ( retainer > 0 ) {translate ([0,0, pulley_b_ht + pulley_t_ht ]) 
		rotate_extrude($fn=teeth*4)  
		polygon([[0,0],[pulley_OD/2,0],[pulley_OD/2 + retainer_ht , retainer_ht],[0 , retainer_ht],[0,0]]);}
		
		if ( idler > 0 ) {translate ([0,0, pulley_b_ht - idler_ht ]) 
		rotate_extrude($fn=teeth*4)  
		polygon([[0,0],[pulley_OD/2 + idler_ht,0],[pulley_OD/2 , idler_ht],[0 , idler_ht],[0,0]]);}
	
		}
	   
		//hole for motor shaft
		translate([0,0,-1])cylinder(r=motor_shaft/2,h=pulley_b_ht + pulley_t_ht + retainer_ht + 2,$fn=motor_shaft*4);
				
		//captive nut and grub screw holes
	
		if ( pulley_b_ht < m3_nut_flats ) { echo ("CAN'T DRAW CAPTIVE NUTS, HEIGHT LESS THAN NUT DIAMETER!!!"); } else {
		if ( (pulley_b_dia - motor_shaft)/2 < m3_nut_depth + 3 ) { echo ("CAN'T DRAW CAPTIVE NUTS, DIAMETER TOO SMALL FOR NUT DEPTH!!!"); } else {
	
			for(j=[1:no_of_nuts]) rotate([0,0,j*nut_angle])
			translate([0,0,nut_elevation])rotate([90,0,0])
	
			union()
			{
				//entrance
				translate([0,-pulley_b_ht/4-0.5,motor_shaft/2+m3_nut_depth/2+nut_shaft_distance]) cube([m3_nut_flats,pulley_b_ht/2+1,m3_nut_depth],center=true);
	
				//nut
				if ( m3_nut_hex > 0 )
					{
						// hex nut
						translate([0,0.25,motor_shaft/2+m3_nut_depth/2+nut_shaft_distance]) rotate([0,0,30]) cylinder(r=m3_nut_points/2,h=m3_nut_depth,center=true,$fn=6);
					} else {
						// square nut
						translate([0,0.25,motor_shaft/2+m3_nut_depth/2+nut_shaft_distance]) cube([m3_nut_flats,m3_nut_flats,m3_nut_depth],center=true);
					}
	
				//grub screw hole
				rotate([0,0,22.5])cylinder(r=m3_dia/2,h=pulley_b_dia/2+1,$fn=8);
			}
		}}
	 }
	   
	}


// Tooth profile modules
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

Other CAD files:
mechanical/assems/pi_standoff.SLDASM
mechanical/assems/control_brd_standoff.SLDASM
mechanical/assems/switch_mounted.SLDASM
mechanical/assems/hopper.SLDASM
mechanical/parts/launcher/unused/motor_pulley_48.scad
mechanical/parts/launcher/unused/motor_pulley_72.scad
mechanical/parts/launcher/unused/launcher_pulley_16.scad
mechanical/assems/battery_mounted.SLDASM
mechanical/assems/dual_flywheel_cage.SLDASM
mechanical/assems/field_supply_side.SLDASM
mechanical/assems/launcher.SLDASM
mechanical/assems/motor_driver_mounted.SLDASM
mechanical/assems/ramp_test.SLDASM
mechanical/assems/unused/flywheel_cage.SLDASM
mechanical/assems/unused/hopper.SLDASM
mechanical/assems/wheel assem.SLDASM
mechanical/field/field_centerwall.SLDPRT
mechanical/field/field_flag.SLDPRT
mechanical/field/field_flagbracket.SLDPRT
mechanical/field/field_floor.SLDPRT
mechanical/field/field_frontpegholder.SLDPRT
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

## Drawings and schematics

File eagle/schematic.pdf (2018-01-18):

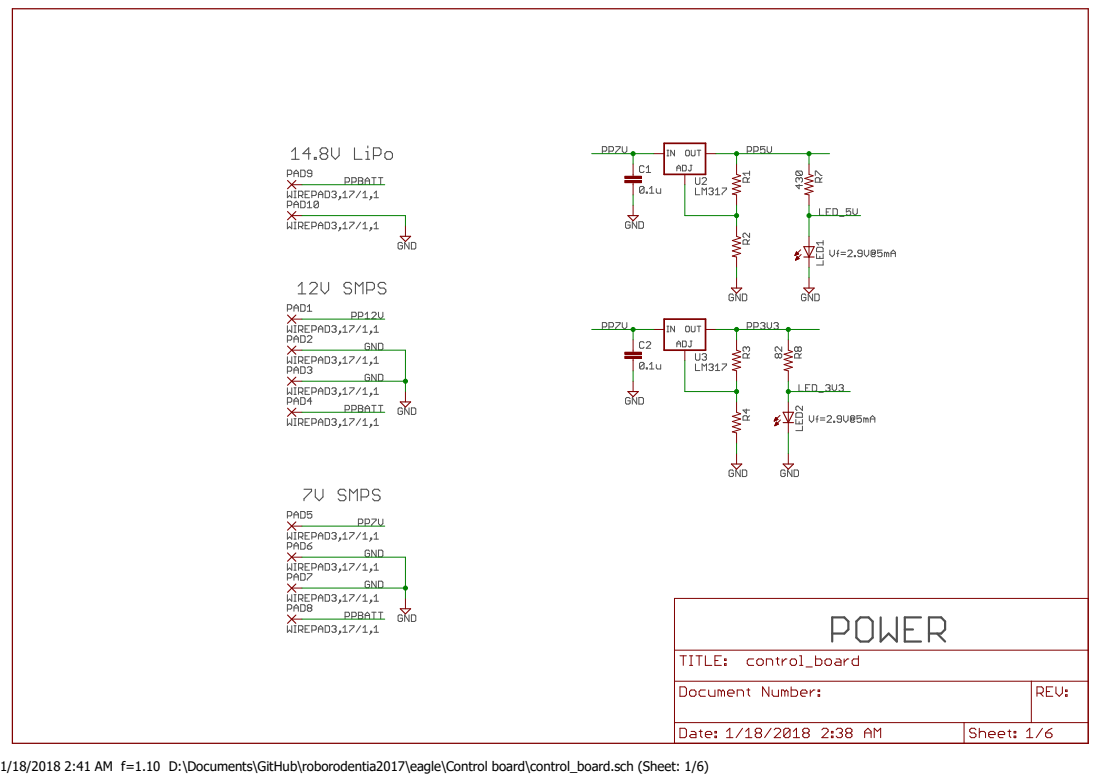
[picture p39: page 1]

1/18/2018 2:41 AM f=1.10 D:\Documents\GitHub\roborodentia2017\eagle\Control board\control_board.sch (Sheet: 1/6)

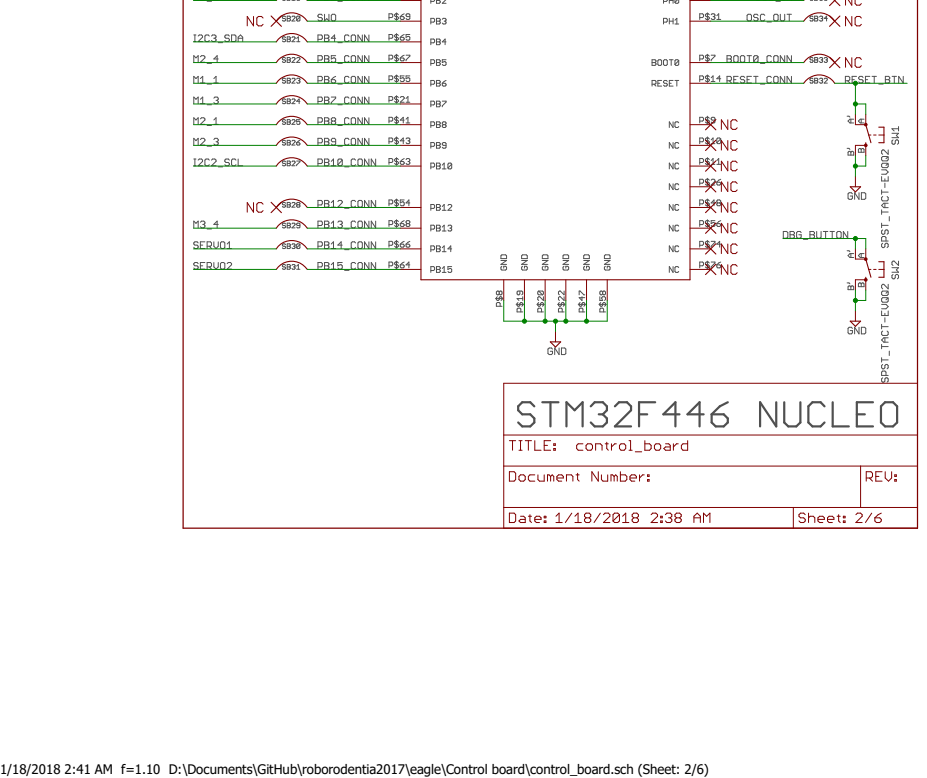
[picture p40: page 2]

1/18/2018 2:41 AM f=1.10 D:\Documents\GitHub\roborodentia2017\eagle\Control board\control_board.sch (Sheet: 2/6)

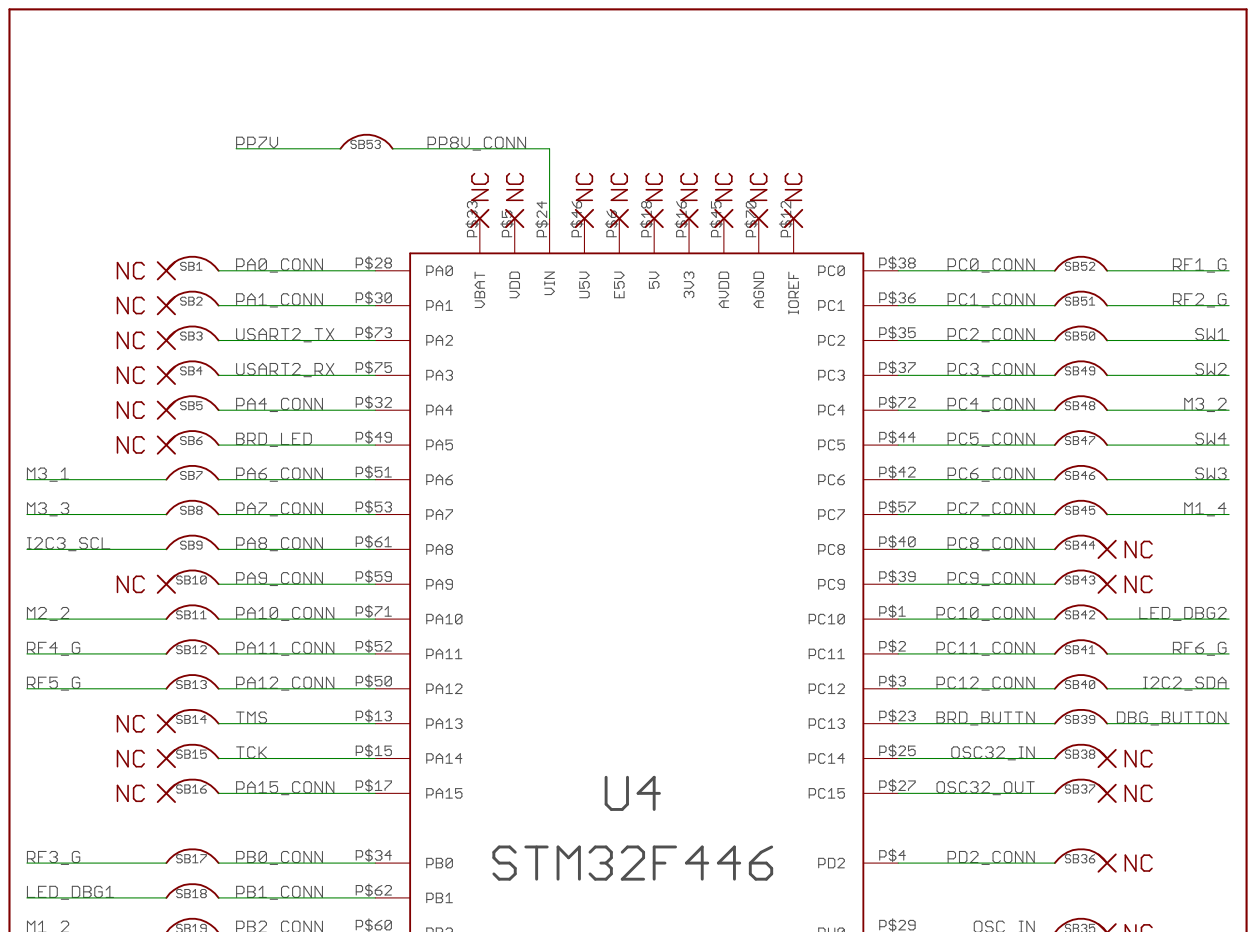
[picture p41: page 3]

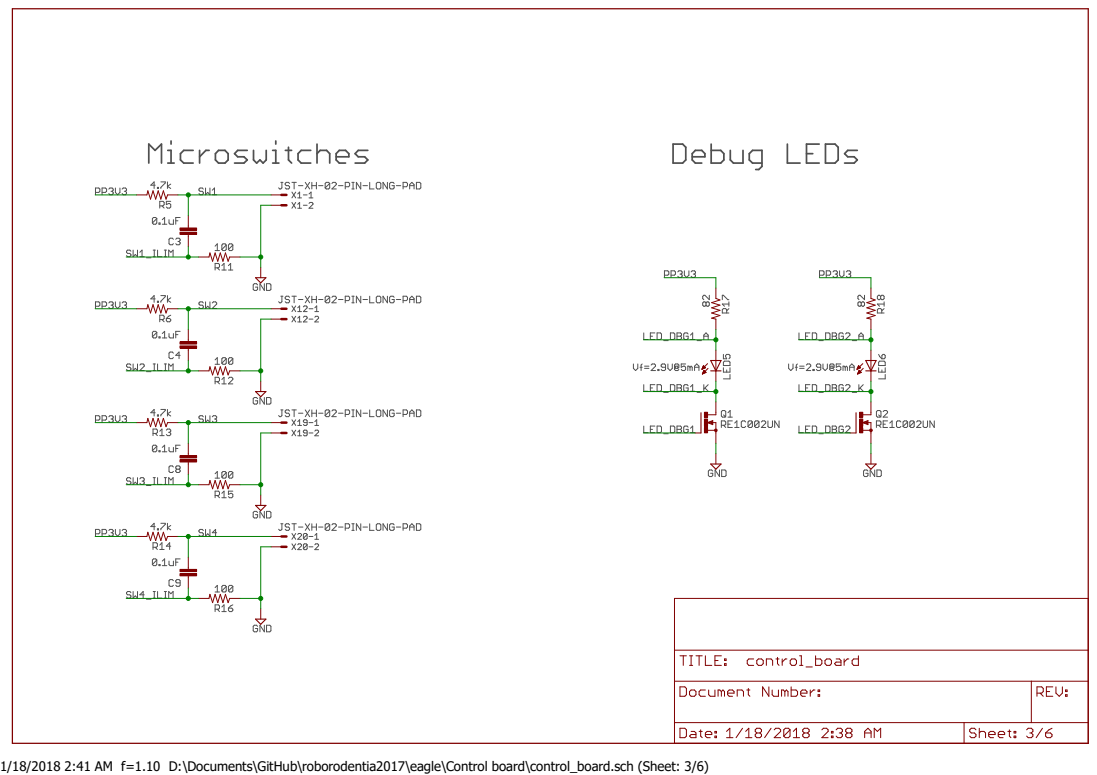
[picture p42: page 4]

1/18/2018 2:41 AM f=1.10 D:\Documents\GitHub\roborodentia2017\eagle\Control board\control_board.sch (Sheet: 3/6)

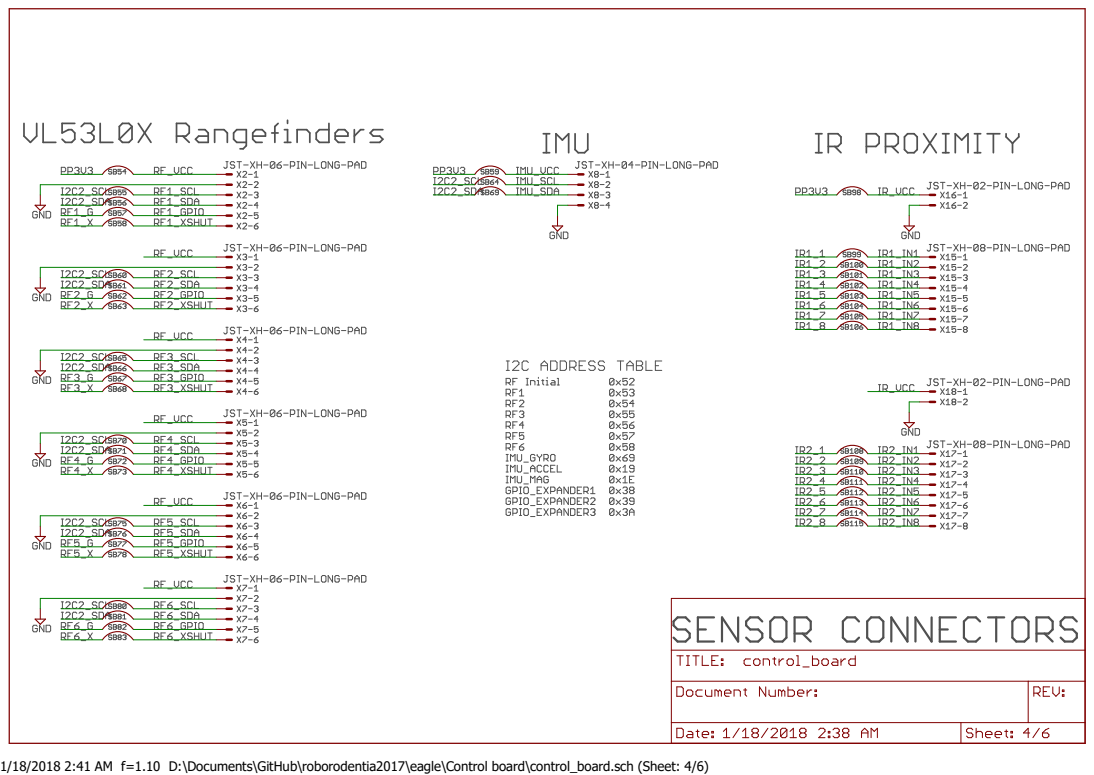
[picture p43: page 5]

1/18/2018 2:41 AM f=1.10 D:\Documents\GitHub\roborodentia2017\eagle\Control board\control_board.sch (Sheet: 4/6)

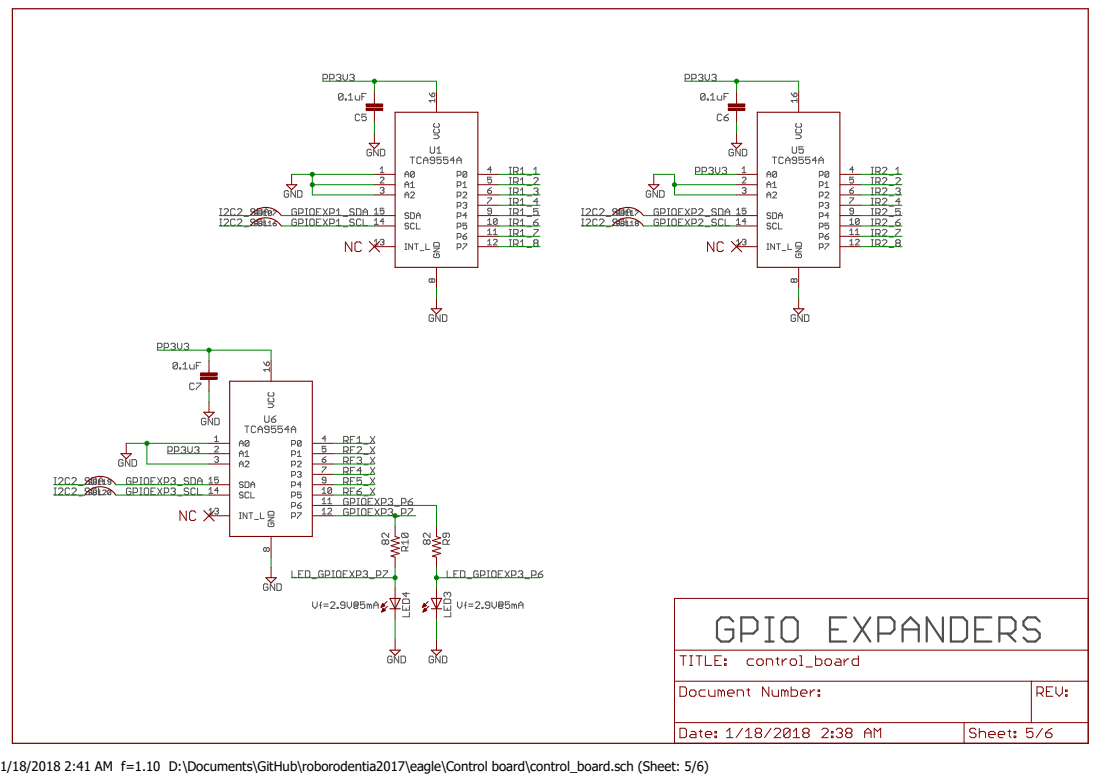
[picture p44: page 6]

1/18/2018 2:41 AM f=1.10 D:\Documents\GitHub\roborodentia2017\eagle\Control board\control_board.sch (Sheet: 5/6)

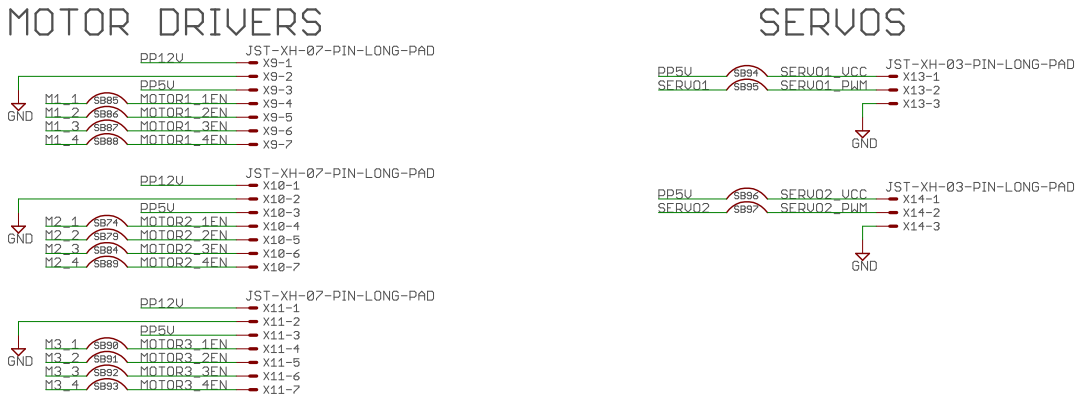
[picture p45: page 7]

1/18/2018 2:41 AM f=1.10 D:\Documents\GitHub\roborodentia2017\eagle\Control board\control_board.sch (Sheet: 6/6)

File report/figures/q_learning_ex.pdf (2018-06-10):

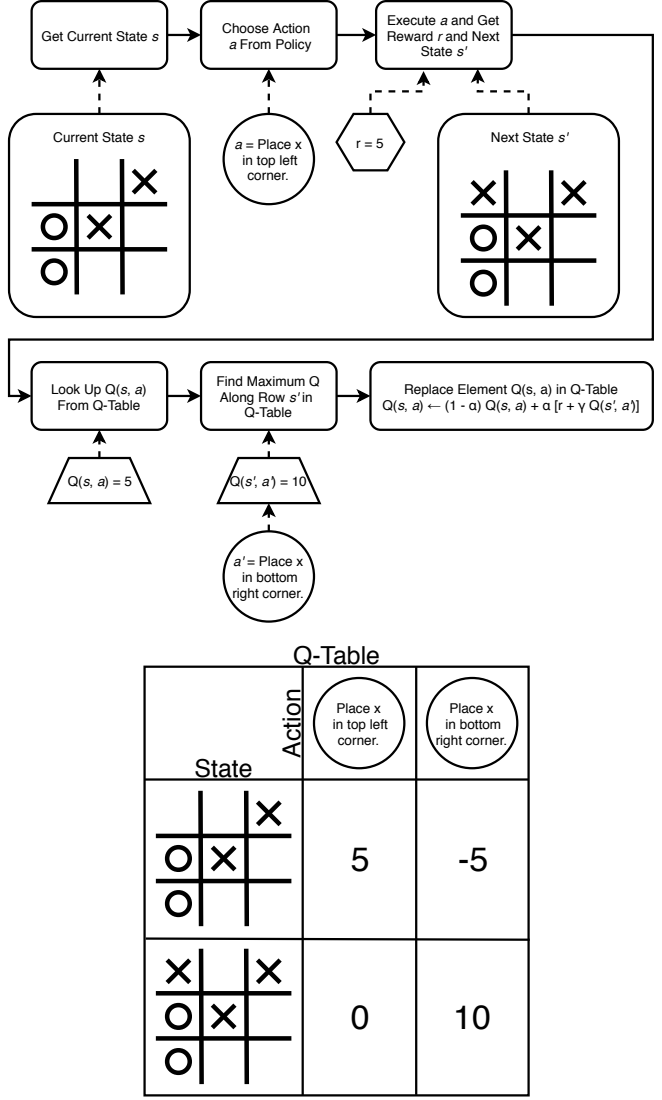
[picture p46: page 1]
Current State s; Next State s'; Choose Action a From Policy; Look Up Q(s, a) From Q-Table; State; Action; Q-Table; Place x in bottom right corner.; a' = Place x in bottom right corner.

Execute a and Get
Reward r and Next
State s'

Get Current State s

a = Place x
in top left
corner.

Find Maximum Q
Along Row s' in
Q-Table

Replace Element Q(s, a) in Q-Table

Place x

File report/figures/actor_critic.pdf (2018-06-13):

## DDPG Network

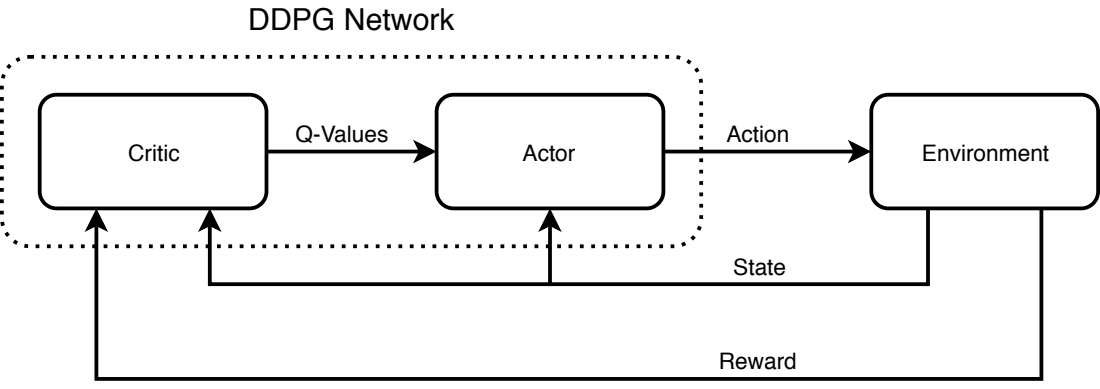
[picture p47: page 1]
Critic; Actor; Environment; State; Reward; Q-Values; Action

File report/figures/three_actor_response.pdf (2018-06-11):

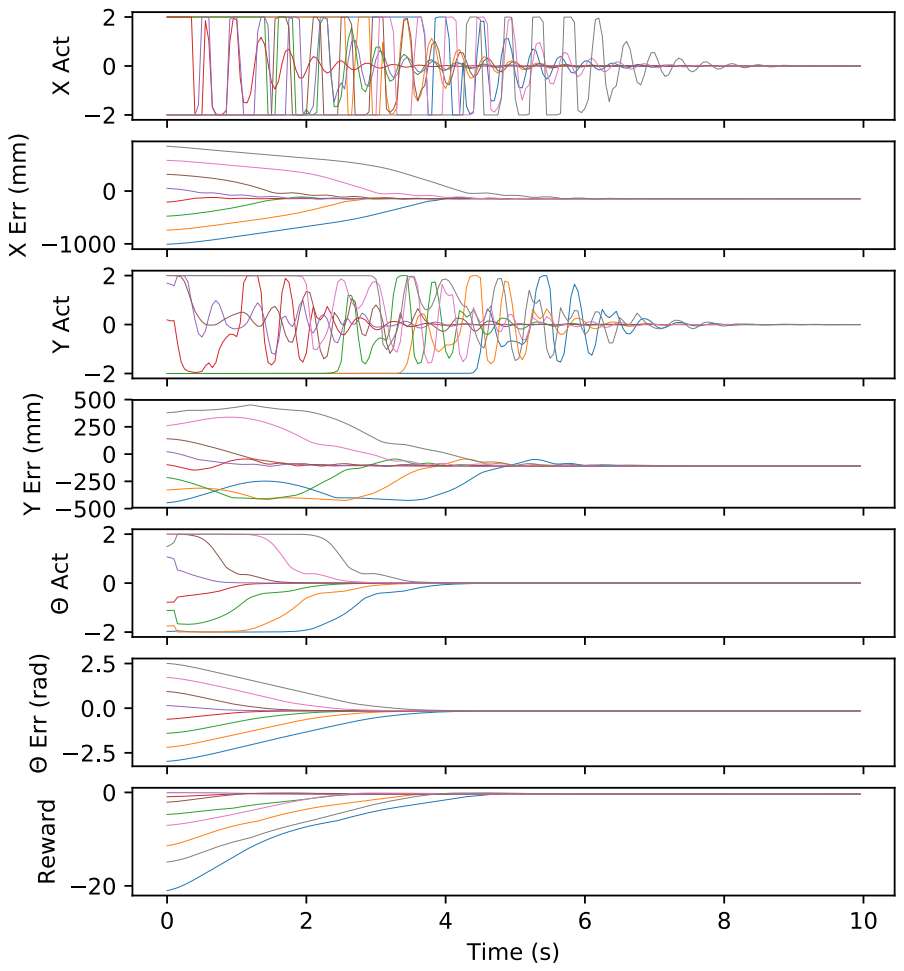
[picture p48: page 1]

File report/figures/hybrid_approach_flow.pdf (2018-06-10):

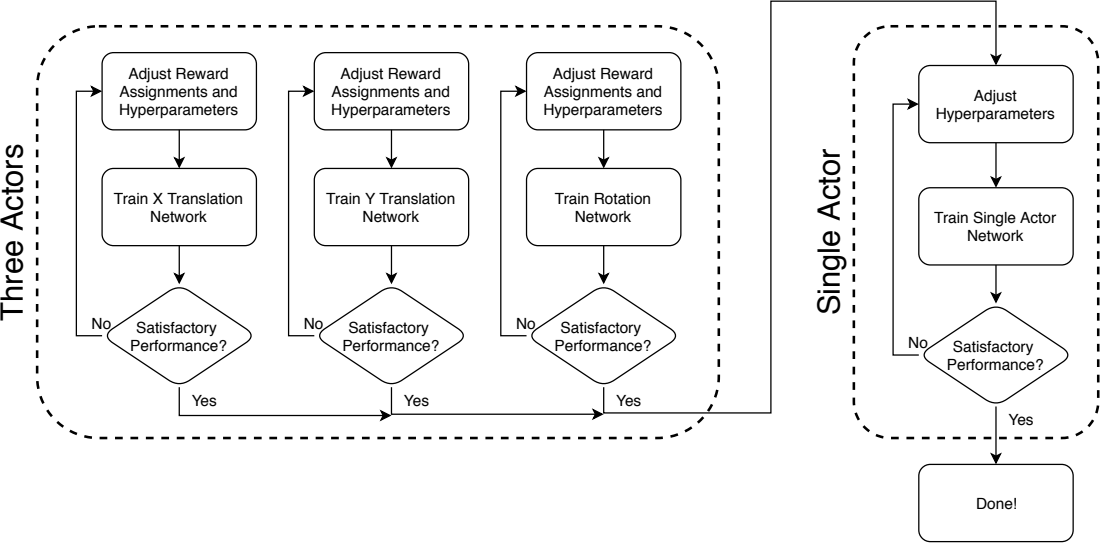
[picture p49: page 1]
Train X Translation Network; Satisfactory Performance?; Adjust Reward Assignments and Hyperparameters; Train Y Translation Network; Train Rotation Network; Yes; Done!; Three Actors; Single Actor; Adjust Hyperparameters

Train Single Actor
Network

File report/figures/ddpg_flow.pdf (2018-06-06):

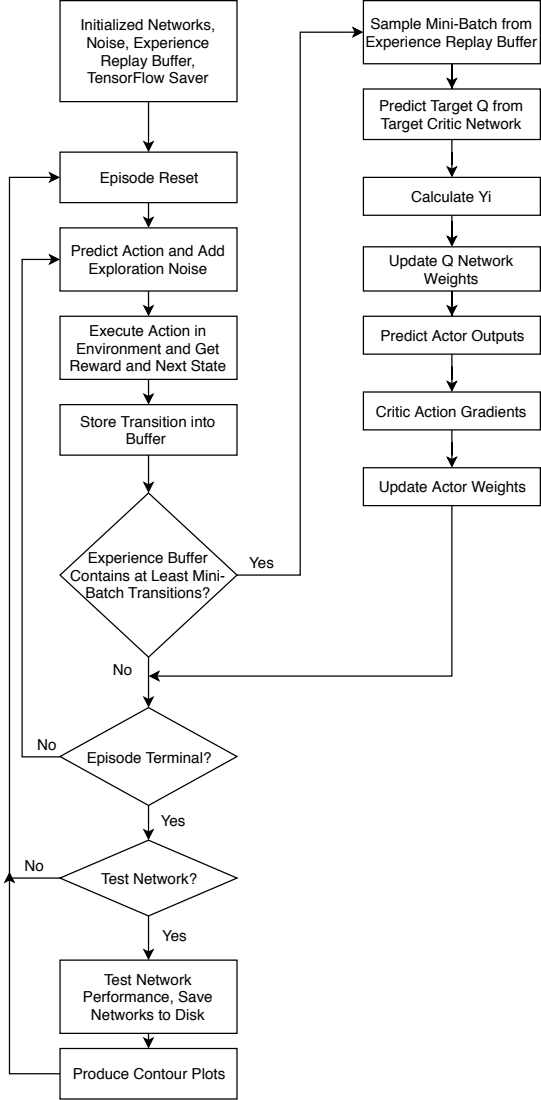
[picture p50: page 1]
Initialized Networks, Noise, Experience Replay Buffer, TensorFlow Saver; Episode Reset; Buffer; Calculate Yi; Update Q Network Weights; Episode Terminal?; Yes; Test Network?

Sample Mini-Batch from
Experience Replay Buffer

Predict Target Q from
Target Critic Network

Predict Action and Add
Exploration Noise

Execute Action in
Environment and Get
Reward and Next State

Predict Actor Outputs

Critic Action Gradients

Store Transition into

Update Actor Weights

Experience Buffer
Contains at Least Mini-
Batch Transitions?

Test Network
Performance, Save
Networks to Disk

Produce Contour Plots

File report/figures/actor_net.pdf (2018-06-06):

# Input

1

s-dim; a-dim; actionbound; Hidden Layer 1; Hidden Layer 2; Output; Layer; Scale; Batch; Norm; ReLU; tanh; Batch Norm

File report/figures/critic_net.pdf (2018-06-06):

1

# State

s-dim; Input; Hidden Layer 1; Hidden Layer 2; Output Layer; a-dim; Action Input; ReLU; Batch; Norm


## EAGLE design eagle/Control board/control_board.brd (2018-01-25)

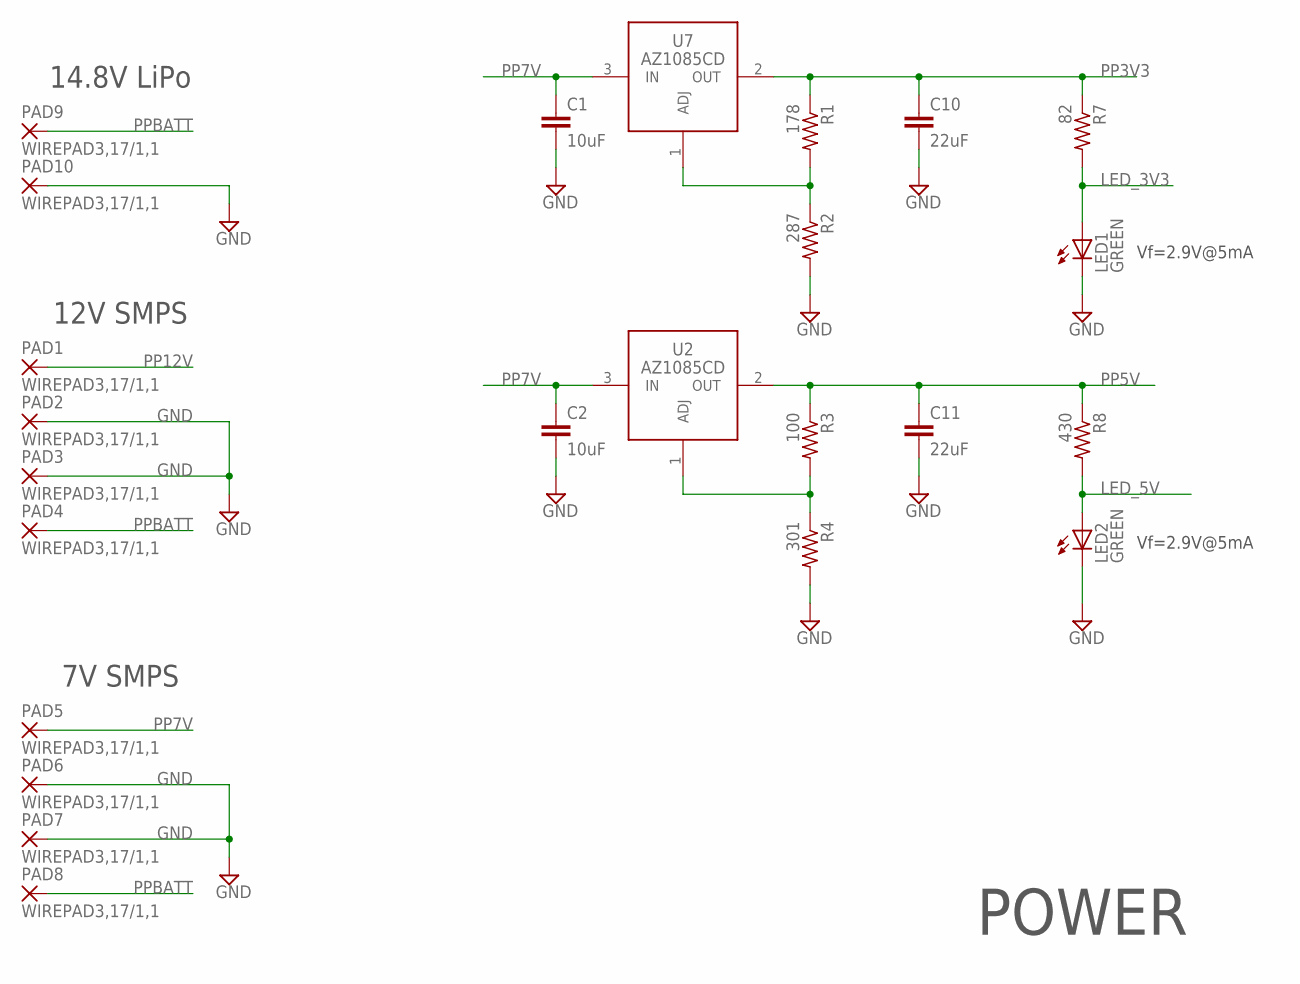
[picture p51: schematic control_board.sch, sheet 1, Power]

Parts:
C1, C2: 10uF; C0603
C10, C11: 22uF; C0603
LED1, LED2: GREEN; CHIPLED_0805; DIGI 732-4971-1-ND
PAD1, PAD2, PAD3, PAD4, PAD5, PAD6, PAD7, PAD8, PAD9, PAD10: WIREPAD3,17/1,1; 3,17/1,1
R1: 178; R0603
R2: 287; R0603
R3: 100; R0603
R4: 301; R0603
R7: 82; R0603
R8: 430; R0603
U2, U7: AZ1085CD; TO252

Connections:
GND: C1.2, C2.2, C10.2, C11.2, LED1.C, LED2.C, PAD2.1, PAD3.1, PAD6.1, PAD7.1, PAD10.1, R2.2, R4.2; also elsewhere on the board
LED_3V3: LED1.A, R7.2
LED_5V: LED2.A, R8.2
unnamed: R3.2, R4.1, U2.1 (ADJ)
unnamed: R1.2, R2.1, U7.1 (ADJ)
PP3V3: C10.1, R1.1, R7.1, U7.2 (OUT); also elsewhere on the board
PP5V: C11.1, R3.1, R8.1, U2.2 (OUT); also elsewhere on the board
PP7V: C1.1, C2.1, PAD5.1, U2.3 (IN), U7.3 (IN); also elsewhere on the board
PP12V: PAD1.1; also elsewhere on the board
PPBATT: PAD4.1, PAD8.1, PAD9.1

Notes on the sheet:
14.8V LiPo
12V SMPS
7V SMPS
Vf=2.9V@5mA
POWER

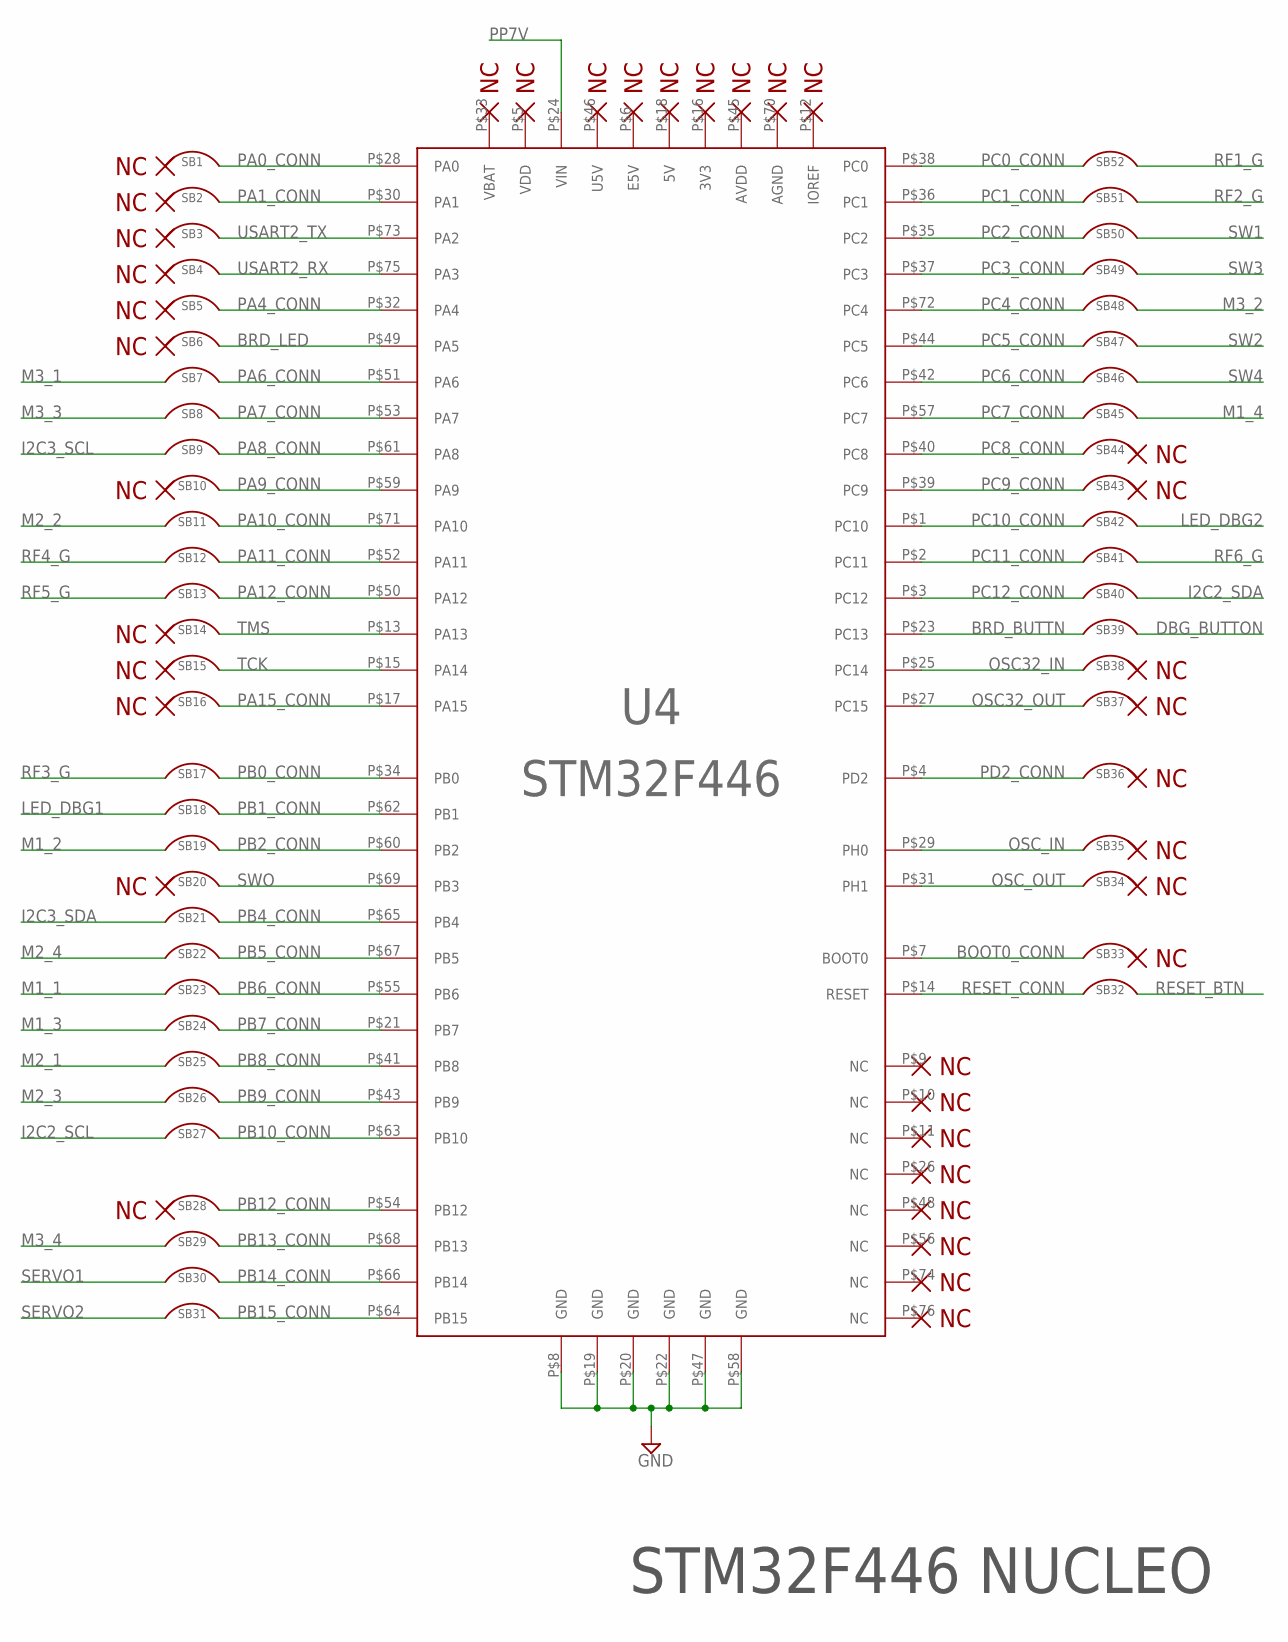
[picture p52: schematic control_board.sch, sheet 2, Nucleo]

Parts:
SB1, SB2, SB3, SB4, SB5, SB6, SB7, SB8, SB9, SB10, SB11, SB12, SB13, SB14, SB15, SB16, SB17, SB18, SB19, SB20, SB21, SB22, SB23, SB24, SB25, SB26, SB27, SB28, SB29, SB30, SB31, SB32, SB33, SB34, SB35, SB36, SB37, SB38, SB39, SB40, SB41, SB42, SB43, SB44, SB45, SB46, SB47, SB48, SB49, SB50, SB51, SB52: SOLDER_BRIDGE
U4: STM32F446; NUCLEO

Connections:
BOOT0_CONN: SB33.P$1, U4.P$7 (BOOT0)
BRD_BUTTN: SB39.P$1, U4.P$23 (PC13)
BRD_LED: SB6.P$2, U4.P$49 (PA5)
DBG_BUTTON: SB39.P$2; also elsewhere on the board
GND: U4.P$8 (GND), U4.P$19 (GND), U4.P$20 (GND), U4.P$22 (GND), U4.P$47 (GND), U4.P$58 (GND); also elsewhere on the board
I2C2_SCL: SB27.P$1; also elsewhere on the board
I2C2_SDA: SB40.P$2; also elsewhere on the board
I2C3_SCL: SB9.P$1; also elsewhere on the board
I2C3_SDA: SB21.P$1; also elsewhere on the board
LED_DBG1: SB18.P$1; also elsewhere on the board
LED_DBG2: SB42.P$2; also elsewhere on the board
M1_1: SB23.P$1; also elsewhere on the board
M1_2: SB19.P$1; also elsewhere on the board
M1_3: SB24.P$1; also elsewhere on the board
M1_4: SB45.P$1; also elsewhere on the board
M2_1: SB25.P$1; also elsewhere on the board
M2_2: SB11.P$1; also elsewhere on the board
M2_3: SB26.P$1; also elsewhere on the board
M2_4: SB22.P$1; also elsewhere on the board
M3_1: SB7.P$1; also elsewhere on the board
M3_2: SB48.P$2; also elsewhere on the board
M3_3: SB8.P$1; also elsewhere on the board
M3_4: SB29.P$1; also elsewhere on the board
OSC32_IN: SB38.P$1, U4.P$25 (PC14)
OSC32_OUT: SB37.P$1, U4.P$27 (PC15)
OSC_IN: SB35.P$1, U4.P$29 (PH0)
OSC_OUT: SB34.P$1, U4.P$31 (PH1)
PA0_CONN: SB1.P$2, U4.P$28 (PA0)
PA1_CONN: SB2.P$2, U4.P$30 (PA1)
PA4_CONN: SB5.P$2, U4.P$32 (PA4)
PA6_CONN: SB7.P$2, U4.P$51 (PA6)
PA7_CONN: SB8.P$2, U4.P$53 (PA7)
PA8_CONN: SB9.P$2, U4.P$61 (PA8)
PA9_CONN: SB10.P$2, U4.P$59 (PA9)
PA10_CONN: SB11.P$2, U4.P$71 (PA10)
PA11_CONN: SB12.P$2, U4.P$52 (PA11)
PA12_CONN: SB13.P$2, U4.P$50 (PA12)
PA15_CONN: SB16.P$2, U4.P$17 (PA15)
PB0_CONN: SB17.P$2, U4.P$34 (PB0)
PB1_CONN: SB18.P$2, U4.P$62 (PB1)
PB2_CONN: SB19.P$2, U4.P$60 (PB2)
PB4_CONN: SB21.P$2, U4.P$65 (PB4)
PB5_CONN: SB22.P$2, U4.P$67 (PB5)
PB6_CONN: SB23.P$2, U4.P$55 (PB6)
PB7_CONN: SB24.P$2, U4.P$21 (PB7)
PB8_CONN: SB25.P$2, U4.P$41 (PB8)
PB9_CONN: SB26.P$2, U4.P$43 (PB9)
PB10_CONN: SB27.P$2, U4.P$63 (PB10)
PB12_CONN: SB28.P$2, U4.P$54 (PB12)
PB13_CONN: SB29.P$2, U4.P$68 (PB13)
PB14_CONN: SB30.P$2, U4.P$66 (PB14)
PB15_CONN: SB31.P$2, U4.P$64 (PB15)
PC0_CONN: SB52.P$2, U4.P$38 (PC0)
PC1_CONN: SB51.P$2, U4.P$36 (PC1)
PC2_CONN: SB50.P$1, U4.P$35 (PC2)
PC3_CONN: SB49.P$1, U4.P$37 (PC3)
PC4_CONN: SB48.P$1, U4.P$72 (PC4)
PC5_CONN: SB47.P$1, U4.P$44 (PC5)
PC6_CONN: SB46.P$1, U4.P$42 (PC6)
PC7_CONN: SB45.P$2, U4.P$57 (PC7)
PC8_CONN: SB44.P$1, U4.P$40 (PC8)
PC9_CONN: SB43.P$2, U4.P$39 (PC9)
PC10_CONN: SB42.P$1, U4.P$1 (PC10)
PC11_CONN: SB41.P$1, U4.P$2 (PC11)
PC12_CONN: SB40.P$1, U4.P$3 (PC12)
PD2_CONN: SB36.P$1, U4.P$4 (PD2)
PP7V: U4.P$24 (VIN); also elsewhere on the board
RESET_BTN: SB32.P$2; also elsewhere on the board
RESET_CONN: SB32.P$1, U4.P$14 (RESET)
RF1_G: SB52.P$1; also elsewhere on the board
RF2_G: SB51.P$1; also elsewhere on the board
RF3_G: SB17.P$1; also elsewhere on the board
RF4_G: SB12.P$1; also elsewhere on the board
RF5_G: SB13.P$1; also elsewhere on the board
RF6_G: SB41.P$2; also elsewhere on the board
SERVO1: SB30.P$1; also elsewhere on the board
SERVO2: SB31.P$1; also elsewhere on the board
SW1: SB50.P$2; also elsewhere on the board
SW2: SB47.P$2; also elsewhere on the board
SW3: SB49.P$2; also elsewhere on the board
SW4: SB46.P$2; also elsewhere on the board
SWO: SB20.P$2, U4.P$69 (PB3)
TCK: SB15.P$2, U4.P$15 (PA14)
TMS: SB14.P$2, U4.P$13 (PA13)
USART2_RX: SB4.P$2, U4.P$75 (PA3)
USART2_TX: SB3.P$2, U4.P$73 (PA2)

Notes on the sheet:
STM32F446 NUCLEO

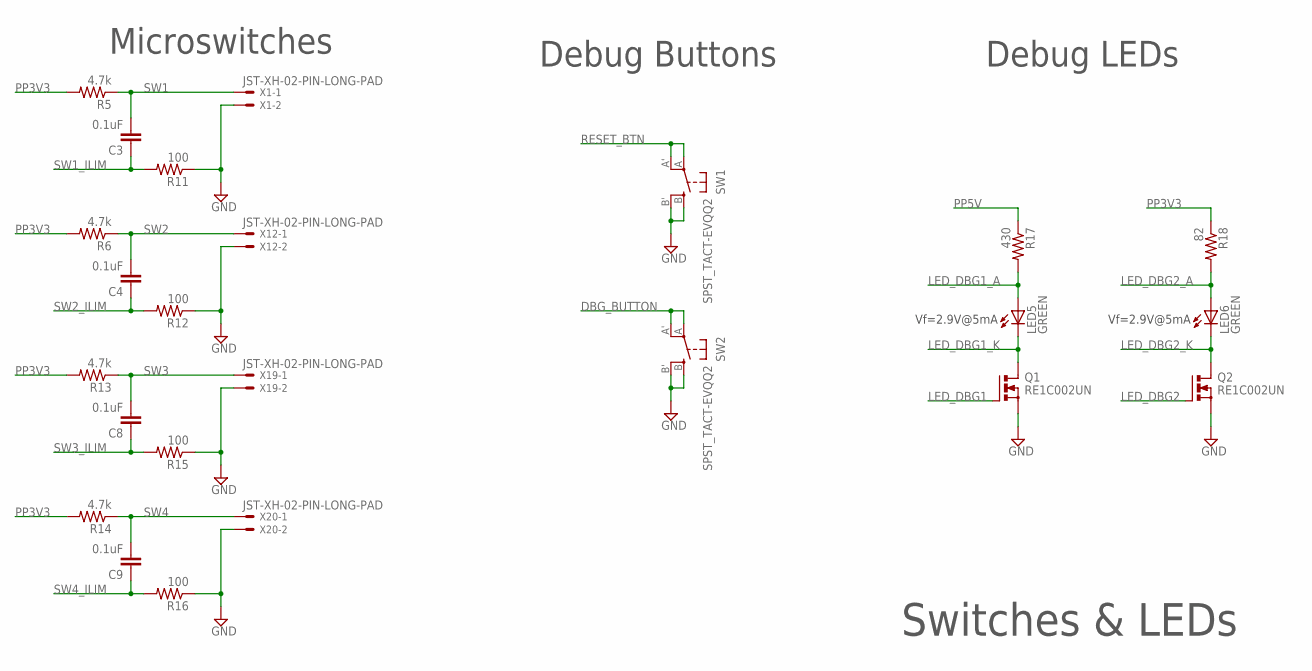
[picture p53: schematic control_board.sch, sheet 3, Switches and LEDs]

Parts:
C3, C4, C8, C9: 0.1uF; C0603
LED5, LED6: GREEN; CHIPLED_0805; DIGI 732-4971-1-ND
Q1, Q2: RE1C002UN; SOT416FL
R5, R6, R13, R14: 4.7k; R0603
R11, R12, R15, R16: 100; R0603
R17: 430; R0603
R18: 82; R0603
SW1, SW2: SPST_TACT-EVQQ2; EVQ-Q2; DIGI P12955SCT-ND
X1, X12, X19, X20: JST-XH-02-PIN-LONG-PAD; JST-XH-02-PACKAGE-LONG-PAD

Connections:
DBG_BUTTON: SW2.A, SW2.A' (P1); also elsewhere on the board
GND: Q1.P$2 (S), Q2.P$2 (S), R11.1, R12.1, R15.1, R16.1, SW1.B (S), SW1.B' (S1), SW2.B (S), SW2.B' (S1), X1.2, X12.2, X19.2, X20.2; also elsewhere on the board
LED_DBG1: Q1.P$1 (G); also elsewhere on the board
LED_DBG1_A: LED5.A, R17.2
LED_DBG1_K: LED5.C, Q1.P$3 (D)
LED_DBG2: Q2.P$1 (G); also elsewhere on the board
LED_DBG2_A: LED6.A, R18.2
LED_DBG2_K: LED6.C, Q2.P$3 (D)
PP3V3: R5.2, R6.2, R13.2, R14.2, R18.1; also elsewhere on the board
PP5V: R17.1; also elsewhere on the board
RESET_BTN: SW1.A, SW1.A' (P1); also elsewhere on the board
SW1: C3.2, R5.1, X1.1; also elsewhere on the board
SW1_ILIM: C3.1, R11.2
SW2: C4.2, R6.1, X12.1; also elsewhere on the board
SW2_ILIM: C4.1, R12.2
SW3: C8.2, R13.1, X19.1; also elsewhere on the board
SW3_ILIM: C8.1, R15.2
SW4: C9.2, R14.1, X20.1; also elsewhere on the board
SW4_ILIM: C9.1, R16.2

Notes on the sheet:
Microswitches
Vf=2.9V@5mA
Debug LEDs
Debug Buttons
Switches & LEDs

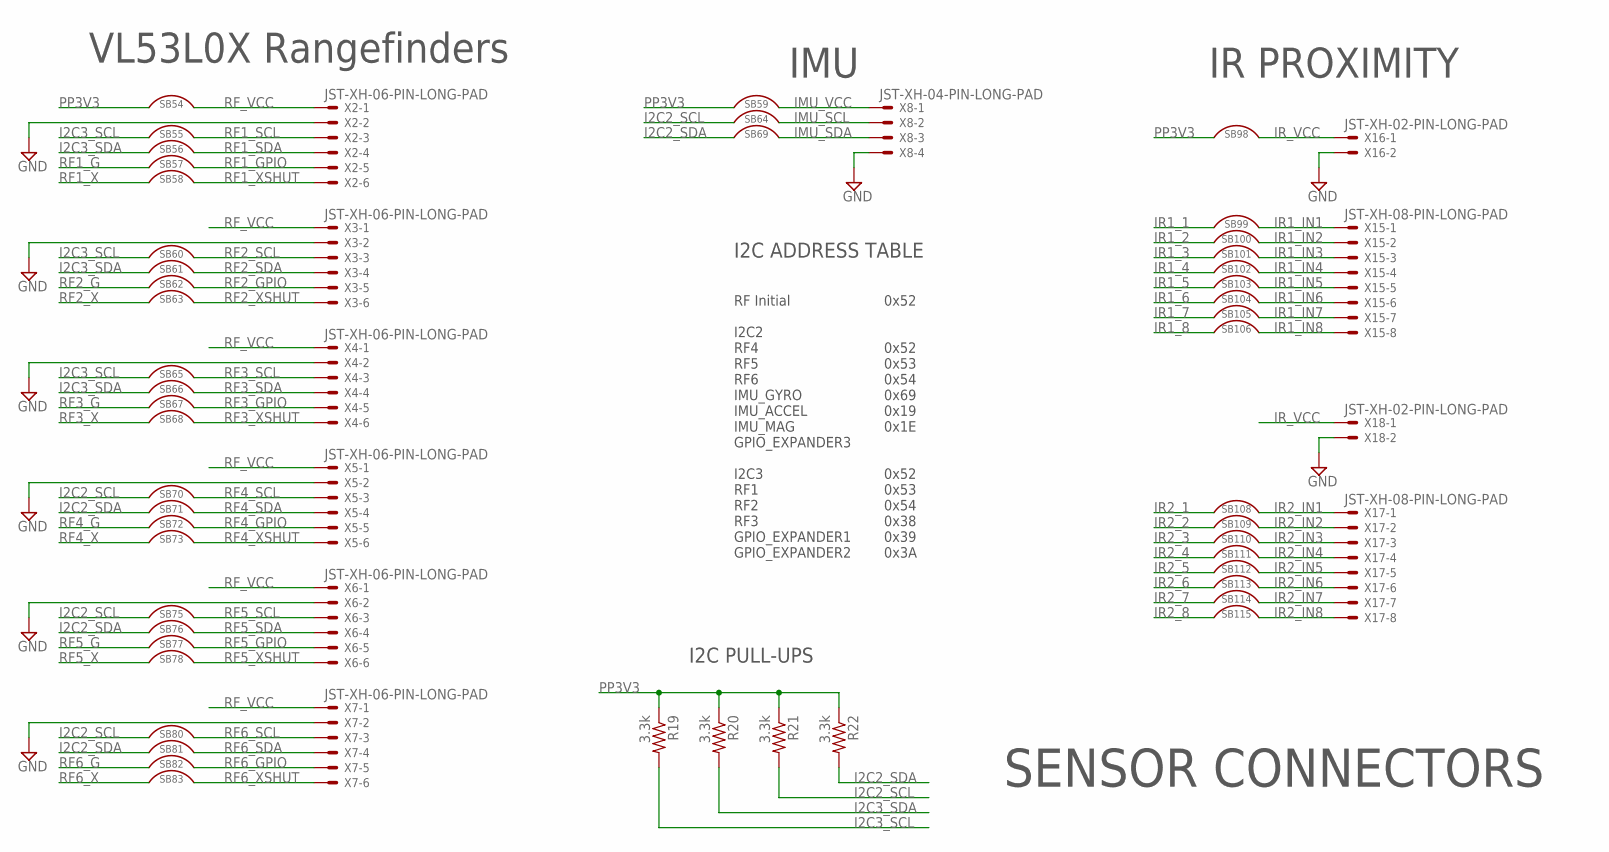
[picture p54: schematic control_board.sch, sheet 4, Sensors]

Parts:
R19, R20, R21, R22: 3.3k; R0603
SB54, SB55, SB56, SB57, SB58, SB59, SB60, SB61, SB62, SB63, SB64, SB65, SB66, SB67, SB68, SB69, SB70, SB71, SB72, SB73, SB75, SB76, SB77, SB78, SB80, SB81, SB82, SB83, SB98, SB99, SB100, SB101, SB102, SB103, SB104, SB105, SB106, SB108, SB109, SB110, SB111, SB112, SB113, SB114, SB115: SOLDER_BRIDGE
X2, X3, X4, X5, X6, X7: JST-XH-06-PIN-LONG-PAD; JST-XH-06-PACKAGE-LONG-PAD
X8: JST-XH-04-PIN-LONG-PAD; JST-XH-04-PACKAGE-LONG-PAD
X15, X17: JST-XH-08-PIN-LONG-PAD; JST-XH-08-PACKAGE-LONG-PAD
X16, X18: JST-XH-02-PIN-LONG-PAD; JST-XH-02-PACKAGE-LONG-PAD

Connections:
GND: X2.2, X3.2, X4.2, X5.2, X6.2, X7.2, X8.4, X16.2, X18.2; also elsewhere on the board
I2C2_SCL: R21.2, SB64.P$1, SB70.P$1, SB75.P$1, SB80.P$1; also elsewhere on the board
I2C2_SDA: R22.2, SB69.P$1, SB71.P$1, SB76.P$1, SB81.P$1; also elsewhere on the board
I2C3_SCL: R19.2, SB55.P$1, SB60.P$1, SB65.P$1; also elsewhere on the board
I2C3_SDA: R20.2, SB56.P$1, SB61.P$1, SB66.P$1; also elsewhere on the board
IMU_SCL: SB64.P$2, X8.2
IMU_SDA: SB69.P$2, X8.3
IMU_VCC: SB59.P$2, X8.1
IR1_1: SB99.P$1; also elsewhere on the board
IR1_2: SB100.P$1; also elsewhere on the board
IR1_3: SB101.P$1; also elsewhere on the board
IR1_4: SB102.P$1; also elsewhere on the board
IR1_5: SB103.P$1; also elsewhere on the board
IR1_6: SB104.P$1; also elsewhere on the board
IR1_7: SB105.P$1; also elsewhere on the board
IR1_8: SB106.P$1; also elsewhere on the board
IR1_IN1: SB99.P$2, X15.1
IR1_IN2: SB100.P$2, X15.2
IR1_IN3: SB101.P$2, X15.3
IR1_IN4: SB102.P$2, X15.4
IR1_IN5: SB103.P$2, X15.5
IR1_IN6: SB104.P$2, X15.6
IR1_IN7: SB105.P$2, X15.7
IR1_IN8: SB106.P$2, X15.8
IR2_1: SB108.P$1; also elsewhere on the board
IR2_2: SB109.P$1; also elsewhere on the board
IR2_3: SB110.P$1; also elsewhere on the board
IR2_4: SB111.P$1; also elsewhere on the board
IR2_5: SB112.P$1; also elsewhere on the board
IR2_6: SB113.P$1; also elsewhere on the board
IR2_7: SB114.P$1; also elsewhere on the board
IR2_8: SB115.P$1; also elsewhere on the board
IR2_IN1: SB108.P$2, X17.1
IR2_IN2: SB109.P$2, X17.2
IR2_IN3: SB110.P$2, X17.3
IR2_IN4: SB111.P$2, X17.4
IR2_IN5: SB112.P$2, X17.5
IR2_IN6: SB113.P$2, X17.6
IR2_IN7: SB114.P$2, X17.7
IR2_IN8: SB115.P$2, X17.8
IR_VCC: SB98.P$2, X16.1, X18.1
PP3V3: R19.1, R20.1, R21.1, R22.1, SB54.P$1, SB59.P$1, SB98.P$1; also elsewhere on the board
RF1_G: SB57.P$1; also elsewhere on the board
RF1_GPIO: SB57.P$2, X2.5
RF1_SCL: SB55.P$2, X2.3
RF1_SDA: SB56.P$2, X2.4
RF1_X: SB58.P$1; also elsewhere on the board
RF1_XSHUT: SB58.P$2, X2.6
RF2_G: SB62.P$1; also elsewhere on the board
RF2_GPIO: SB62.P$2, X3.5
RF2_SCL: SB60.P$2, X3.3
RF2_SDA: SB61.P$2, X3.4
RF2_X: SB63.P$1; also elsewhere on the board
RF2_XSHUT: SB63.P$2, X3.6
RF3_G: SB67.P$1; also elsewhere on the board
RF3_GPIO: SB67.P$2, X4.5
RF3_SCL: SB65.P$2, X4.3
RF3_SDA: SB66.P$2, X4.4
RF3_X: SB68.P$1; also elsewhere on the board
RF3_XSHUT: SB68.P$2, X4.6
RF4_G: SB72.P$1; also elsewhere on the board
RF4_GPIO: SB72.P$2, X5.5
RF4_SCL: SB70.P$2, X5.3
RF4_SDA: SB71.P$2, X5.4
RF4_X: SB73.P$1; also elsewhere on the board
RF4_XSHUT: SB73.P$2, X5.6
RF5_G: SB77.P$1; also elsewhere on the board
RF5_GPIO: SB77.P$2, X6.5
RF5_SCL: SB75.P$2, X6.3
RF5_SDA: SB76.P$2, X6.4
RF5_X: SB78.P$1; also elsewhere on the board
RF5_XSHUT: SB78.P$2, X6.6
RF6_G: SB82.P$1; also elsewhere on the board
RF6_GPIO: SB82.P$2, X7.5
RF6_SCL: SB80.P$2, X7.3
RF6_SDA: SB81.P$2, X7.4
RF6_X: SB83.P$1; also elsewhere on the board
RF6_XSHUT: SB83.P$2, X7.6
RF_VCC: SB54.P$2, X2.1, X3.1, X4.1, X5.1, X6.1, X7.1

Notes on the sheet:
VL53L0X Rangefinders
IMU
IR PROXIMITY
I2C ADDRESS TABLE
SENSOR CONNECTORS
RF Initial I2C2 RF4 RF5 RF6 IMU_GYRO IMU_ACCEL IMU_MAG GPIO_EXPANDER3 I2C3 RF1 RF2 RF3 GPIO_EXPANDER1 GPIO_EXPANDER2
0x52 0x52 0x53 0x54 0x69 0x19 0x1E 0x52 0x53 0x54 0x38 0x39 0x3A
I2C PULL-UPS

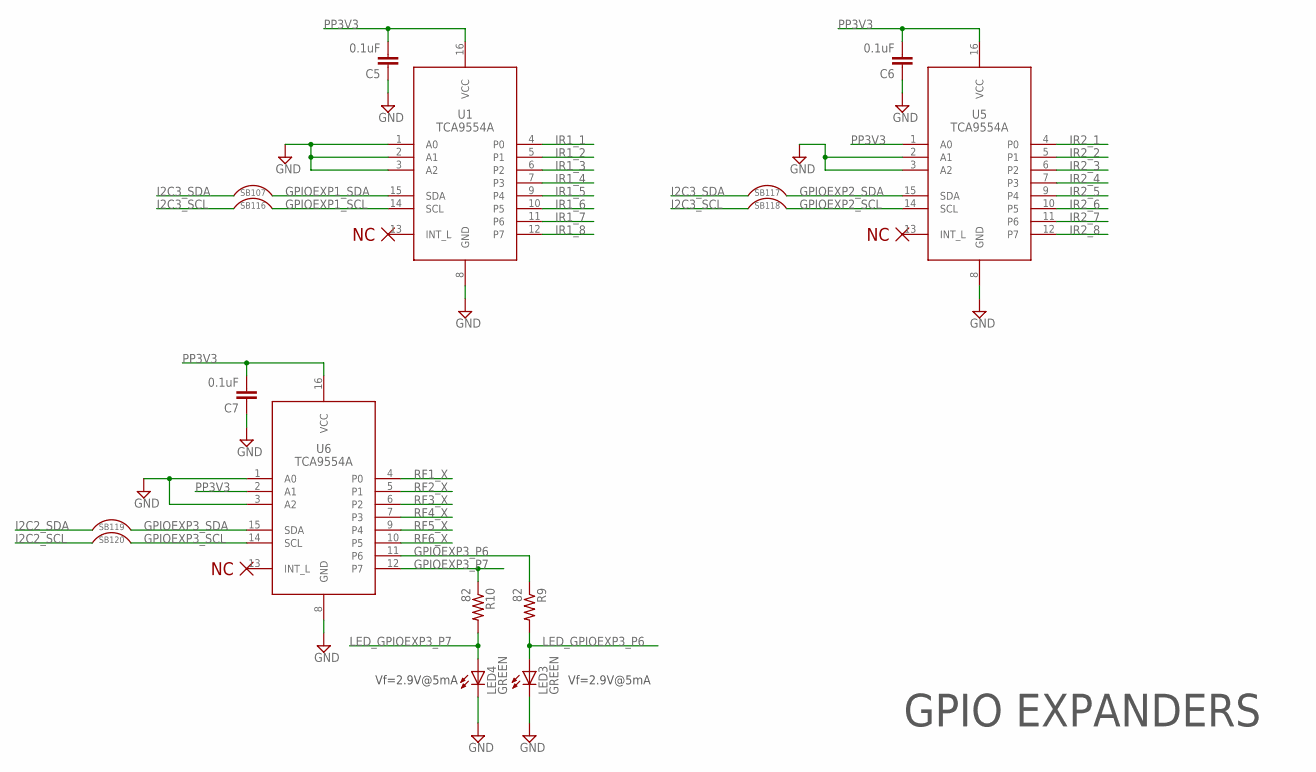
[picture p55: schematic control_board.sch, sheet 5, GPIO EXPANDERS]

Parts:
C5, C6, C7: 0.1uF; C0603
LED3, LED4: GREEN; CHIPLED_0805; DIGI 732-4971-1-ND
R9, R10: 82; R0603
SB107, SB116, SB117, SB118, SB119, SB120: SOLDER_BRIDGE
U1, U5, U6: TCA9554A; SOIC16-1.27-10.2X7.5MM

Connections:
GND: C5.1, C6.1, C7.1, LED3.C, LED4.C, U1.1 (A0), U1.2 (A1), U1.3 (A2), U1.8 (GND), U5.2 (A1), U5.3 (A2), U5.8 (GND), U6.1 (A0), U6.3 (A2), U6.8 (GND); also elsewhere on the board
GPIOEXP1_SCL: SB116.P$2, U1.14 (SCL)
GPIOEXP1_SDA: SB107.P$2, U1.15 (SDA)
GPIOEXP2_SCL: SB118.P$2, U5.14 (SCL)
GPIOEXP2_SDA: SB117.P$2, U5.15 (SDA)
GPIOEXP3_P6: R9.1, U6.11 (P6)
GPIOEXP3_P7: R10.1, U6.12 (P7)
GPIOEXP3_SCL: SB120.P$2, U6.14 (SCL)
GPIOEXP3_SDA: SB119.P$2, U6.15 (SDA)
I2C2_SCL: SB120.P$1; also elsewhere on the board
I2C2_SDA: SB119.P$1; also elsewhere on the board
I2C3_SCL: SB116.P$1, SB118.P$1; also elsewhere on the board
I2C3_SDA: SB107.P$1, SB117.P$1; also elsewhere on the board
IR1_1: U1.4 (P0); also elsewhere on the board
IR1_2: U1.5 (P1); also elsewhere on the board
IR1_3: U1.6 (P2); also elsewhere on the board
IR1_4: U1.7 (P3); also elsewhere on the board
IR1_5: U1.9 (P4); also elsewhere on the board
IR1_6: U1.10 (P5); also elsewhere on the board
IR1_7: U1.11 (P6); also elsewhere on the board
IR1_8: U1.12 (P7); also elsewhere on the board
IR2_1: U5.4 (P0); also elsewhere on the board
IR2_2: U5.5 (P1); also elsewhere on the board
IR2_3: U5.6 (P2); also elsewhere on the board
IR2_4: U5.7 (P3); also elsewhere on the board
IR2_5: U5.9 (P4); also elsewhere on the board
IR2_6: U5.10 (P5); also elsewhere on the board
IR2_7: U5.11 (P6); also elsewhere on the board
IR2_8: U5.12 (P7); also elsewhere on the board
LED_GPIOEXP3_P6: LED3.A, R9.2
LED_GPIOEXP3_P7: LED4.A, R10.2
PP3V3: C5.2, C6.2, C7.2, U1.16 (VCC), U5.1 (A0), U5.16 (VCC), U6.2 (A1), U6.16 (VCC); also elsewhere on the board
RF1_X: U6.4 (P0); also elsewhere on the board
RF2_X: U6.5 (P1); also elsewhere on the board
RF3_X: U6.6 (P2); also elsewhere on the board
RF4_X: U6.7 (P3); also elsewhere on the board
RF5_X: U6.9 (P4); also elsewhere on the board
RF6_X: U6.10 (P5); also elsewhere on the board

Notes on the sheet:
GPIO EXPANDERS
Vf=2.9V@5mA

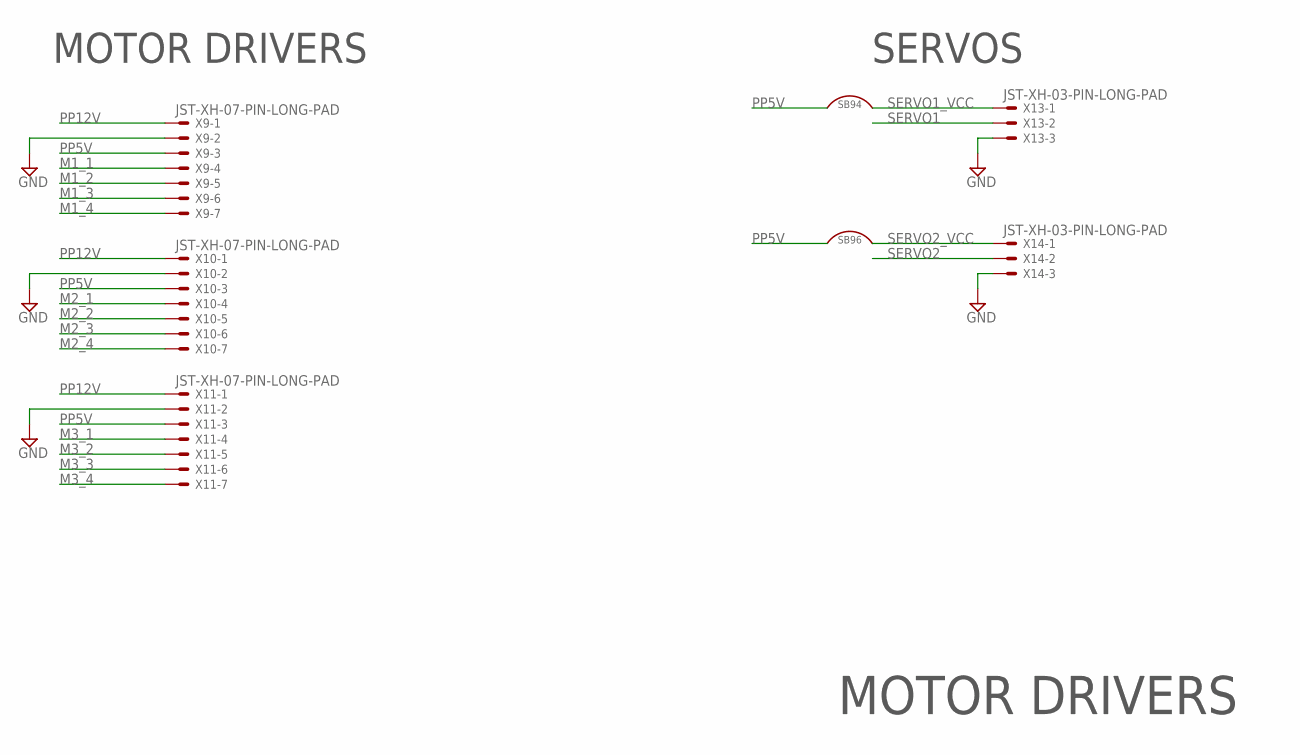
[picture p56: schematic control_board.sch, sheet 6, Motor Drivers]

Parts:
SB94, SB96: SOLDER_BRIDGE
X9, X10, X11: JST-XH-07-PIN-LONG-PAD; JST-XH-07-PACKAGE-LONG-PAD
X13, X14: JST-XH-03-PIN-LONG-PAD; JST-XH-03-PACKAGE-LONG-PAD

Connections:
GND: X9.2, X10.2, X11.2, X13.3, X14.3; also elsewhere on the board
M1_1: X9.4; also elsewhere on the board
M1_2: X9.5; also elsewhere on the board
M1_3: X9.6; also elsewhere on the board
M1_4: X9.7; also elsewhere on the board
M2_1: X10.4; also elsewhere on the board
M2_2: X10.5; also elsewhere on the board
M2_3: X10.6; also elsewhere on the board
M2_4: X10.7; also elsewhere on the board
M3_1: X11.4; also elsewhere on the board
M3_2: X11.5; also elsewhere on the board
M3_3: X11.6; also elsewhere on the board
M3_4: X11.7; also elsewhere on the board
PP5V: SB94.P$1, SB96.P$1, X9.3, X10.3, X11.3; also elsewhere on the board
PP12V: X9.1, X10.1, X11.1; also elsewhere on the board
SERVO1: X13.2; also elsewhere on the board
SERVO1_VCC: SB94.P$2, X13.1
SERVO2: X14.2; also elsewhere on the board
SERVO2_VCC: SB96.P$2, X14.1

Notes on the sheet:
MOTOR DRIVERS
SERVOS

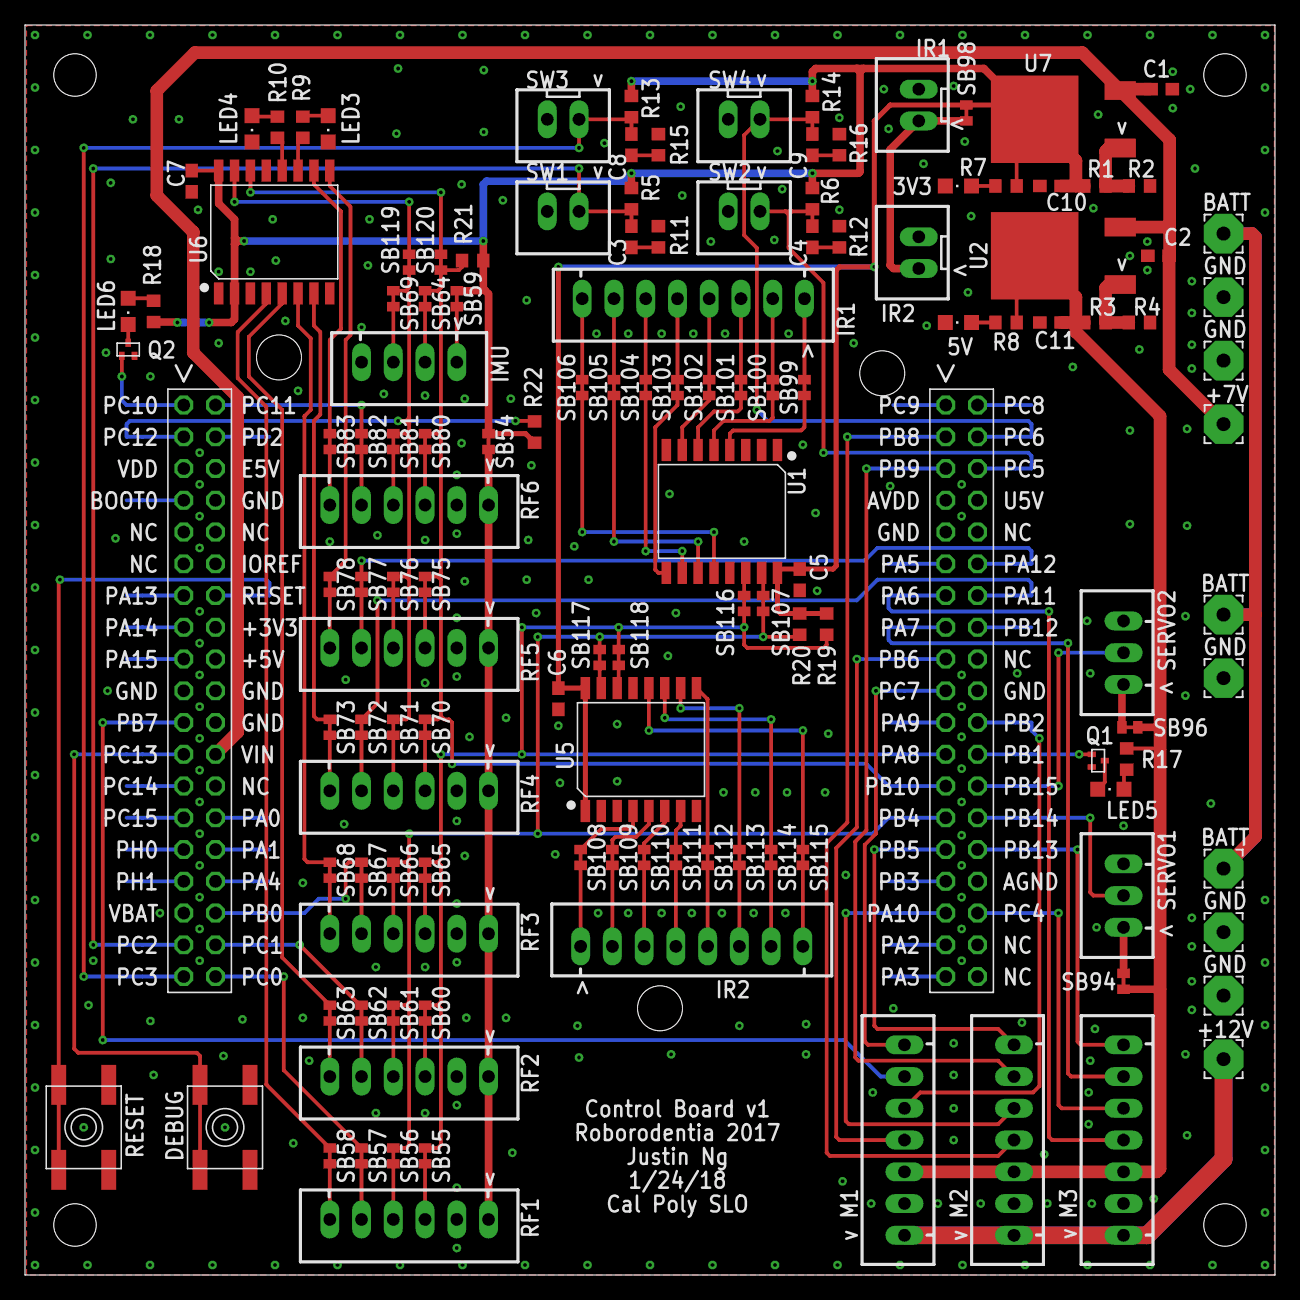
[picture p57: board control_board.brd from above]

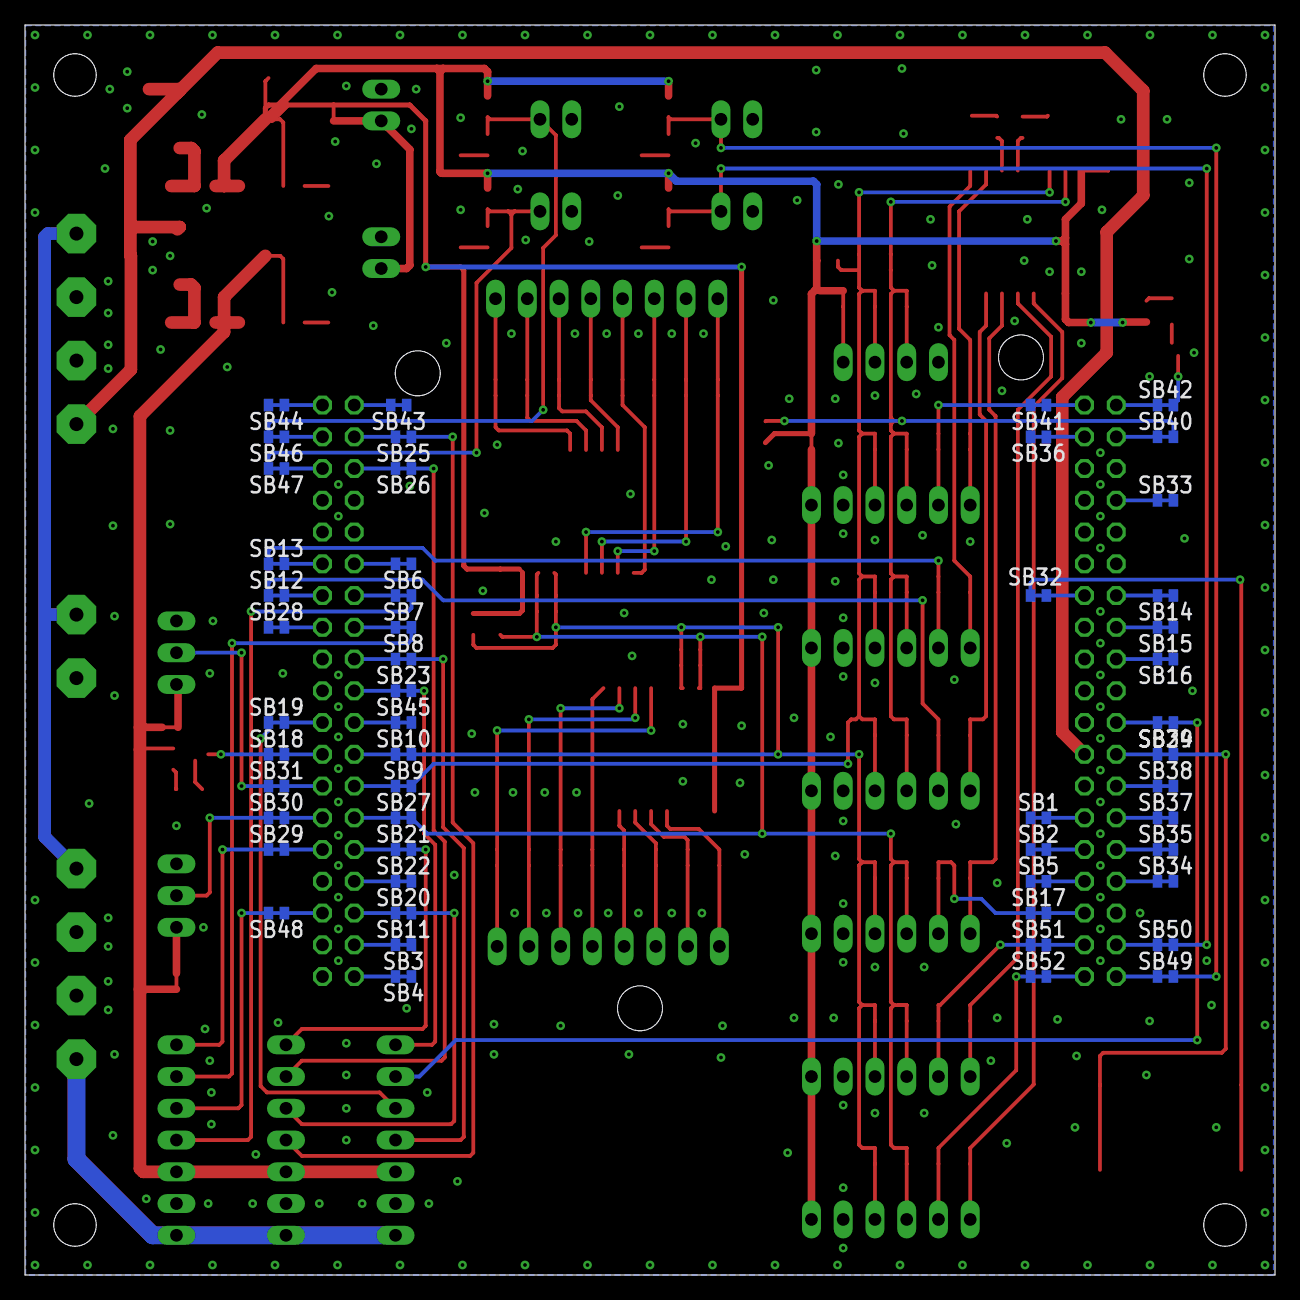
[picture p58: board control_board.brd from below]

Board: 2 copper layers, 100.0 x 100.0 mm, 184 parts (52 on the bottom side), 181 nets.

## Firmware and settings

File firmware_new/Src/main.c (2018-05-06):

/**
  ******************************************************************************
  * File Name          : main.c
  * Description        : Main program body
  ******************************************************************************
  ** This notice applies to any and all portions of this file
  * that are not between comment pairs USER CODE BEGIN and
  * USER CODE END. Other portions of this file, whether 
  * inserted by the user or by software development tools
  * are owned by their respective copyright owners.
  *
  * COPYRIGHT(c) 2018 STMicroelectronics
  *
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
  ******************************************************************************
  */

/* Includes ------------------------------------------------------------------*/
#include "main.h"
#include "stm32f4xx_hal.h"
#include "dma.h"
#include "i2c.h"
#include "tim.h"
#include "usart.h"
#include "gpio.h"

/* USER CODE BEGIN Includes */
#include <stdlib.h>
#include <stdio.h>
#include "imu.h"
#include "vl53l0x_top.h"
/* USER CODE END Includes */


/* USER CODE BEGIN PV */
struct motor_t {
    GPIO_TypeDef *GPIOx;
    uint16_t GPIO_Pin;
    GPIO_PinState PinState;

    TIM_HandleTypeDef *TIM_Handle;
    TIM_OC_InitTypeDef sConfigOC;
    uint32_t TIM_Channel;
};

struct motor_t motorConfigs[4] = { 
    {MOTOR_FL_DIR_GPIO_Port, MOTOR_FL_DIR_Pin, GPIO_PIN_RESET, 0, {0}, TIM_CHANNEL_2}, 
    {MOTOR_FR_DIR_GPIO_Port, MOTOR_FR_DIR_Pin, GPIO_PIN_RESET, 0, {0}, TIM_CHANNEL_4}, 
    {MOTOR_BR_DIR_GPIO_Port, MOTOR_BR_DIR_Pin, GPIO_PIN_RESET, 0, {0}, TIM_CHANNEL_1}, 
    {MOTOR_BL_DIR_GPIO_Port, MOTOR_BL_DIR_Pin, GPIO_PIN_RESET, 0, {0}, TIM_CHANNEL_3}}; 
struct motor_t* motorConfigsPtr = motorConfigs;

volatile uint8_t wd_reset = 0;

uint8_t data_updating = 0;
unsigned char data_packet[21];
volatile uint8_t sensor_update_req = 0;
volatile uint8_t dbg_btn_latch = 0;

// WARNING!! Do not spam the UART or else Raspberry PI doesn't communicate well
//#define DATA_PRINT_EN
//
/* USER CODE END PV */

void SystemClock_Config(void);

/* USER CODE BEGIN PFP */
void TimeStamp_Reset();
uint32_t TimeStamp_Get();

/* USER CODE END PFP */

int main(void)
{

  /* USER CODE BEGIN 1 */

    // Initialize all clocks so we don't run into weird clock problems...
    RCC->AHB1ENR |= 0xFFFFFFFF;
    RCC->AHB2ENR |= 0xFFFFFFFF;
    RCC->AHB3ENR |= 0xFFFFFFFF;
    RCC->APB1ENR |= 0xFFFFFFFF;
    RCC->APB2ENR |= 0xFFFFFFFF;

  /* USER CODE END 1 */

  /* MCU Configuration----------------------------------------------------------*/

  /* Reset of all peripherals, Initializes the Flash interface and the Systick. */
  HAL_Init();

  /* Configure the system clock */
  SystemClock_Config();

  /* USER CODE BEGIN 2 */
    /* Initialize all configured peripherals */
    MX_GPIO_Init();
    MX_DMA_Init();
    MX_I2C2_Init();
    MX_I2C3_Init();
    MX_TIM3_Init();
    MX_TIM4_Init();
    MX_TIM12_Init();
    MX_USART2_UART_Init();
    MX_TIM5_Init();

    TIM_OC_InitTypeDef sConfigOC;
    sConfigOC.OCMode = TIM_OCMODE_PWM1;
    sConfigOC.OCPolarity = TIM_OCPOLARITY_HIGH;
    sConfigOC.OCFastMode = TIM_OCFAST_DISABLE;
    sConfigOC.Pulse = 0;

    int i;
    for (i=0; i<4; i++) {
        motorConfigs[i].TIM_Handle = &htim4; 
        motorConfigs[i].sConfigOC = sConfigOC; 
    }

    TimeStamp_Reset();
    serviceUART();
    printf("Enabling IMU...\r\n");
    IMU_begin();
    printf("Initializing rangefinders...\r\n");
    VL53L0X_begin();

    // Set servo default position
//    sConfigOC.Pulse = SERVO1_PULSE_2;
//    if (HAL_TIM_PWM_ConfigChannel(&htim12, &sConfigOC, TIM_CHANNEL_1) != HAL_OK) { Error_Handler(); }
    if (HAL_TIM_PWM_Start(&htim12, TIM_CHANNEL_1) != HAL_OK){ Error_Handler(); }

  /* USER CODE END 2 */

  /* Infinite loop */
  /* USER CODE BEGIN WHILE */
    uint32_t wd_start = 0;
    uint32_t cur_time = 0;
    uint8_t wd_en = 0;
    data_packet[20] = '\n';

    while (1)
    {
  /* USER CODE END WHILE */

  /* USER CODE BEGIN 3 */

        // Reset watchdog start time if flag is set
        if (wd_reset == 1){
            wd_start = TimeStamp_Get();  // Units of 0.1 ms based on Timer5
            wd_en = 1;
            wd_reset = 0;
        } else if (wd_en == 1){
            // Trigger if watchdog is enabled and expires
            cur_time = TimeStamp_Get();
            if ((cur_time - wd_start) > WD_LEN){
                wd_en = 0;

                // Disable motors
                int i;
                for (i=0; i<4; i++) {
                    motorConfigs[i].PinState = GPIO_PIN_RESET;
                    motorConfigs[i].sConfigOC.Pulse = 0; 
                }
                for (i=0; i<4; i++) {
                    // Alter the PWM duty cycle and start PWM again
                    if (HAL_TIM_PWM_ConfigChannel(motorConfigs[i].TIM_Handle, &motorConfigs[i].sConfigOC,
                               motorConfigs[i].TIM_Channel) != HAL_OK) { Error_Handler(); }
                    if (HAL_TIM_PWM_Start(motorConfigs[i].TIM_Handle, motorConfigs[i].TIM_Channel)
                            != HAL_OK){ Error_Handler(); }

                    // Set the direction pin
                    HAL_GPIO_WritePin(motorConfigs[i].GPIOx, motorConfigs[i].GPIO_Pin, motorConfigs[i].PinState);
                }
            }
        }

        // Read debug button
        dbg_btn_latch = HAL_GPIO_ReadPin(B1_GPIO_Port, B1_Pin) && dbg_btn_latch;

        if (sensor_update_req == 1){
            int i;
            for (i = 0; i < 4; i++){
                if (rangefinderRead(i)){
                    data_packet[i*2  ] = (rangeData[i] >> 8) & 0xFF;
                    data_packet[i*2+1] =  rangeData[i]       & 0xFF;
                }
            }
            sensor_update_req = 0;
        }

        magnetometer_read();
        data_packet[ 8] = (magData.x >> 8) & 0xFF;
        data_packet[ 9] =  magData.x       & 0xFF;
        data_packet[10] = (magData.y >> 8) & 0xFF;
        data_packet[11] =  magData.y       & 0xFF;
        data_packet[12] = (magData.z >> 8) & 0xFF;
        data_packet[13] =  magData.z       & 0xFF;

        accelerometer_read();
        data_packet[14] = (accelData.x >> 8) & 0xFF;
        data_packet[15] =  accelData.x       & 0xFF;
        data_packet[16] = (accelData.y >> 8) & 0xFF;
        data_packet[17] =  accelData.y       & 0xFF;
        data_packet[18] = (accelData.z >> 8) & 0xFF;
        data_packet[19] =  accelData.z       & 0xFF;

    //        gyro_read();
//        data_packet[20] = (gyroData.x >> 8) & 0xFF;
//        data_packet[21] =  gyroData.x       & 0xFF;
//        data_packet[22] = (gyroData.y >> 8) & 0xFF;
//        data_packet[23] =  gyroData.y       & 0xFF;
//        data_packet[24] = (gyroData.z >> 8) & 0xFF;
//        data_packet[25] =  gyroData.z       & 0xFF;
//
    }
  /* USER CODE END 3 */

}

/** System Clock Configuration
*/
void SystemClock_Config(void)
{

  RCC_OscInitTypeDef RCC_OscInitStruct;
  RCC_ClkInitTypeDef RCC_ClkInitStruct;

    /**Configure the main internal regulator output voltage 
    */
  __HAL_RCC_PWR_CLK_ENABLE();

  __HAL_PWR_VOLTAGESCALING_CONFIG(PWR_REGULATOR_VOLTAGE_SCALE1);

    /**Initializes the CPU, AHB and APB busses clocks 
    */
  RCC_OscInitStruct.OscillatorType = RCC_OSCILLATORTYPE_HSE;
  RCC_OscInitStruct.HSEState = RCC_HSE_ON;
  RCC_OscInitStruct.PLL.PLLState = RCC_PLL_ON;
  RCC_OscInitStruct.PLL.PLLSource = RCC_PLLSOURCE_HSE;
  RCC_OscInitStruct.PLL.PLLM = 8;
  RCC_OscInitStruct.PLL.PLLN = 360;
  RCC_OscInitStruct.PLL.PLLP = RCC_PLLP_DIV2;
  RCC_OscInitStruct.PLL.PLLQ = 2;
  RCC_OscInitStruct.PLL.PLLR = 2;
  if (HAL_RCC_OscConfig(&RCC_OscInitStruct) != HAL_OK)
  {
    _Error_Handler(__FILE__, __LINE__);
  }

    /**Activate the Over-Drive mode 
    */
  if (HAL_PWREx_EnableOverDrive() != HAL_OK)
  {
    _Error_Handler(__FILE__, __LINE__);
  }

    /**Initializes the CPU, AHB and APB busses clocks 
    */
  RCC_ClkInitStruct.ClockType = RCC_CLOCKTYPE_HCLK|RCC_CLOCKTYPE_SYSCLK
                              |RCC_CLOCKTYPE_PCLK1|RCC_CLOCKTYPE_PCLK2;
  RCC_ClkInitStruct.SYSCLKSource = RCC_SYSCLKSOURCE_PLLCLK;
  RCC_ClkInitStruct.AHBCLKDivider = RCC_SYSCLK_DIV1;
  RCC_ClkInitStruct.APB1CLKDivider = RCC_HCLK_DIV4;
  RCC_ClkInitStruct.APB2CLKDivider = RCC_HCLK_DIV2;

  if (HAL_RCC_ClockConfig(&RCC_ClkInitStruct, FLASH_LATENCY_5) != HAL_OK)
  {
    _Error_Handler(__FILE__, __LINE__);
  }

    /**Configure the Systick interrupt time 
    */
  HAL_SYSTICK_Config(HAL_RCC_GetHCLKFreq()/1000);

    /**Configure the Systick 
    */
  HAL_SYSTICK_CLKSourceConfig(SYSTICK_CLKSOURCE_HCLK);

  /* SysTick_IRQn interrupt configuration */
  HAL_NVIC_SetPriority(SysTick_IRQn, 0, 0);
}

/* USER CODE BEGIN 4 */
void TimeStamp_Reset(){
    HAL_TIM_Base_Start(&htim5);
    htim5.Instance->CNT=0;
}

uint32_t TimeStamp_Get(){
    return htim5.Instance->CNT;
}

// Redirect printf to UART
int _write (int fd, char *ptr, int len) 
{ 
    transmitUART(ptr, len);
    return len; 
}

// Execute a command from the console
void consoleCommand(uint8_t *ptr, int len)
{
    uint32_t timestart; 
    uint32_t timestop; 
    timestart = TimeStamp_Get();
    wd_reset = 1;

    // V for version
    if (ptr[0] == 'V' || ptr[0] == 'v'){
        printf("Robojustin v0.2\r\n");
    }

    // I for I2C bus scan
    else if (ptr[0] == 'I' || ptr[0] == 'i'){
        // I2C2
        if (ptr[1] == '2'){
            I2C_Scan(&hi2c2);
        }
        // I2C3
        if (ptr[1] == '3'){
            I2C_Scan(&hi2c3);
        }
    }

    // A for queue sensor read
    else if (ptr[0] == 'A' || ptr[0] == 'a') {
        sensor_update_req = 1;
    }

    // B for send data in binary
    else if (ptr[0] == 'B' || ptr[0] == 'b') {
        transmitUART(data_packet, 21);
    }
     
    // Z for send data in binary
    else if (ptr[0] == 'Z' || ptr[0] == 'z') {
        printf("%d\n", dbg_btn_latch);
        dbg_btn_latch = 1;
    }

    // D for send data in human readable format
    else if (ptr[0] == 'D' || ptr[0] == 'd') {
        printf("%d,%d,%d,%d,%d,%d,%d,%d,%d,%d,%d,%d,%d\r\n", 
                rangeData[0], rangeData[1], 
                rangeData[2], rangeData[3], 
                magData.x, magData.y, magData.z,
                accelData.x, accelData.y, accelData.z, 
                gyroData.x, gyroData.y, gyroData.z);
    }
    
    // M for motor control commands
    else if (ptr[0] == 'M' || ptr[0] == 'm'){  
        int i;
        int32_t val;
        int32_t motorU[4];
        sscanf (ptr,"%*s %d %d %d %d", &motorU[0], &motorU[1], &motorU[2], &motorU[3]);
//        printf ("%d %d %d %d\n", motorU[0], motorU[1], motorU[2], motorU[3]);

        for (i=0; i<4; i++) {
            if (motorU[i] < 0){
                motorConfigs[i].PinState = GPIO_PIN_SET;
                motorConfigs[i].sConfigOC.Pulse = 2047 + motorU[i]; 
            } else {
                motorConfigs[i].PinState = GPIO_PIN_RESET;
                motorConfigs[i].sConfigOC.Pulse = motorU[i]; 
            }
        }

        for (i=0; i<4; i++) {
            // Alter the PWM duty cycle and start PWM again
            if (HAL_TIM_PWM_ConfigChannel(motorConfigs[i].TIM_Handle, &motorConfigs[i].sConfigOC,
                       motorConfigs[i].TIM_Channel) != HAL_OK) { Error_Handler(); }
            if (HAL_TIM_PWM_Start(motorConfigs[i].TIM_Handle, motorConfigs[i].TIM_Channel)
                    != HAL_OK){ Error_Handler(); }
            // Set the direction pin
            HAL_GPIO_WritePin(motorConfigs[i].GPIOx, motorConfigs[i].GPIO_Pin, motorConfigs[i].PinState);
        }
    }
    // S for servo commands
    else if (ptr[0] == 'S' || ptr[0] == 's'){  
        TIM_OC_InitTypeDef sConfigOC;
        sConfigOC.OCMode = TIM_OCMODE_PWM1;
        sConfigOC.OCPolarity = TIM_OCPOLARITY_HIGH;
        sConfigOC.OCFastMode = TIM_OCFAST_DISABLE;

        if (ptr[1] == '0'){         // Set servo to 0 degrees
            sConfigOC.Pulse = SERVO1_PULSE_1;
        }
        else if (ptr[1] == '1'){    // Set servo to slot 1 release
            sConfigOC.Pulse = SERVO1_PULSE_1;
        }
        else if (ptr[1] == '2'){    // Set servo to slot 2 release
            sConfigOC.Pulse = SERVO1_PULSE_2;
        }
        else if (ptr[1] == '3'){    // Set servo to slot 3 release
            sConfigOC.Pulse = SERVO1_PULSE_3;
        }
        else if (ptr[1] == '4'){    // Set servo to slot 4 release
            sConfigOC.Pulse = SERVO1_PULSE_4;
        }

        if (ptr[2] == 'S' || ptr[2] == 's'){  
            sConfigOC.Pulse = atoi((char *)ptr + 3);
        }

        // Alter the PWM duty cycle and start PWM again
        if (HAL_TIM_PWM_ConfigChannel(&htim12, &sConfigOC, TIM_CHANNEL_1) != HAL_OK) { Error_Handler(); }
        if (HAL_TIM_PWM_Start(&htim12, TIM_CHANNEL_1) != HAL_OK){ Error_Handler(); }
    }
    // L for launcher macro commands
    else if (ptr[0] == 'L' || ptr[0] == 'l'){  
        uint32_t slot_pulse1 = SERVO1_PULSE_90;
        uint32_t slot_pulse2 = SERVO1_PULSE_90;

        // Fire left side slots
        if (ptr[1] == 'L' || ptr[1] == 'l'){    
            slot_pulse1 = SERVO1_PULSE_2;
            slot_pulse2 = SERVO1_PULSE_1;
        }
        // Fire right side slots 
        else if (ptr[1] == 'R' || ptr[1] == 'r'){    
            slot_pulse1 = SERVO1_PULSE_3;
            slot_pulse2 = SERVO1_PULSE_4;
        }
        // Stop    
        else if (ptr[1] == 'S' || ptr[1] == 's'){    
            // Disable blower and launcher motors
            HAL_GPIO_WritePin(BLOWER_DIR_GPIO_Port, BLOWER_DIR_Pin, 0);
            HAL_GPIO_WritePin(MOTOR_LAUNCH_DIR_GPIO_Port, MOTOR_LAUNCH_DIR_Pin, 0);
        }

        if (ptr[1] == 'L' || ptr[1] == 'l' || ptr[1] == 'R' || ptr[1] == 'r'){
            uint32_t cur_time = 0;
            uint32_t cur_time2 = 0;
            uint32_t wiggle_amt = 200;
            uint32_t wiggle_period = 1200;

            TIM_OC_InitTypeDef sConfigOC;
            sConfigOC.OCMode = TIM_OCMODE_PWM1;
            sConfigOC.OCPolarity = TIM_OCPOLARITY_HIGH;
            sConfigOC.OCFastMode = TIM_OCFAST_DISABLE;

            // Enable blower and launcher motors
            HAL_GPIO_WritePin(BLOWER_DIR_GPIO_Port, BLOWER_DIR_Pin, 1);
            sConfigOC.Pulse = 130;
            if (HAL_TIM_PWM_ConfigChannel(&htim3, &sConfigOC, TIM_CHANNEL_2) != HAL_OK) { Error_Handler(); }
            if (HAL_TIM_PWM_Start(&htim3, TIM_CHANNEL_2) != HAL_OK){ Error_Handler(); }
            HAL_GPIO_WritePin(MOTOR_LAUNCH_DIR_GPIO_Port, MOTOR_LAUNCH_DIR_Pin, 1);

            // Wait for balls to finish firing first slot
            cur_time = TimeStamp_Get();
            while (TimeStamp_Get() - cur_time < 25000){
                // Move servo to release first slot and jiggle it
                sConfigOC.Pulse = slot_pulse1 + wiggle_amt;
                if (HAL_TIM_PWM_ConfigChannel(&htim12, &sConfigOC, TIM_CHANNEL_1) != HAL_OK) { Error_Handler(); }
                if (HAL_TIM_PWM_Start(&htim12, TIM_CHANNEL_1) != HAL_OK){ Error_Handler(); }

                cur_time2 = TimeStamp_Get();
                while (TimeStamp_Get() - cur_time2 < wiggle_period){}

                sConfigOC.Pulse = slot_pulse1 - wiggle_amt;
                if (HAL_TIM_PWM_ConfigChannel(&htim12, &sConfigOC, TIM_CHANNEL_1) != HAL_OK) { Error_Handler(); }
                if (HAL_TIM_PWM_Start(&htim12, TIM_CHANNEL_1) != HAL_OK){ Error_Handler(); }

                cur_time2 = TimeStamp_Get();
                while (TimeStamp_Get() - cur_time2 < wiggle_period){}
            }

            // Wait for balls to finish firing second slot
            cur_time = TimeStamp_Get();
            while (TimeStamp_Get() - cur_time < 25000){
                // Move servo to release first slot and jiggle it
                sConfigOC.Pulse = slot_pulse2 + wiggle_amt;
                if (HAL_TIM_PWM_ConfigChannel(&htim12, &sConfigOC, TIM_CHANNEL_1) != HAL_OK) { Error_Handler(); }
                if (HAL_TIM_PWM_Start(&htim12, TIM_CHANNEL_1) != HAL_OK){ Error_Handler(); }

                cur_time2 = TimeStamp_Get();
                while (TimeStamp_Get() - cur_time2 < wiggle_period){}

                sConfigOC.Pulse = slot_pulse2 - wiggle_amt;
                if (HAL_TIM_PWM_ConfigChannel(&htim12, &sConfigOC, TIM_CHANNEL_1) != HAL_OK) { Error_Handler(); }
                if (HAL_TIM_PWM_Start(&htim12, TIM_CHANNEL_1) != HAL_OK){ Error_Handler(); }

                cur_time2 = TimeStamp_Get();
                while (TimeStamp_Get() - cur_time2 < wiggle_period){}
            }

            // Disable blower and launcher motors
            HAL_GPIO_WritePin(BLOWER_DIR_GPIO_Port, BLOWER_DIR_Pin, 0);
            sConfigOC.Pulse = 0;
            if (HAL_TIM_PWM_ConfigChannel(&htim3, &sConfigOC, TIM_CHANNEL_2) != HAL_OK) { Error_Handler(); }
            if (HAL_TIM_PWM_Start(&htim3, TIM_CHANNEL_2) != HAL_OK){ Error_Handler(); }
            HAL_GPIO_WritePin(MOTOR_LAUNCH_DIR_GPIO_Port, MOTOR_LAUNCH_DIR_Pin, 0);

            // Move servo to center position
            sConfigOC.Pulse = SERVO1_PULSE_90;
            if (HAL_TIM_PWM_ConfigChannel(&htim12, &sConfigOC, TIM_CHANNEL_1) != HAL_OK) { Error_Handler(); }
            if (HAL_TIM_PWM_Start(&htim12, TIM_CHANNEL_1) != HAL_OK){ Error_Handler(); }
        }
    }
    timestop = TimeStamp_Get();
//    printf("%d\n", (timestop - timestart));
}            
/* USER CODE END 4 */
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


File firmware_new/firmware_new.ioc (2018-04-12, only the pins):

Mcu.UserName=STM32F446RETx
PA10.GPIO_Label=M2_2
PA10.Signal=GPIO_Output
PA11.GPIO_Label=RF4_G
PA11.Signal=GPXTI11
PA12.GPIO_Label=RF5_G
PA12.Signal=GPXTI12
PA13.GPIO_Label=TMS
PA13.Signal=SYS_JTMS-SWDIO
PA14.GPIO_Label=TCK
PA14.Signal=SYS_JTCK-SWCLK
PA2.GPIO_Label=USART_TX
PA2.Signal=USART2_TX
PA3.GPIO_Label=USART_RX
PA3.Signal=USART2_RX
PA5.GPIO_Label=LD2 [Green Led]
PA5.Signal=GPIO_Output
PA6.GPIO_Label=M3_1
PA6.Signal=S_TIM3_CH1
PA7.GPIO_Label=M3_3
PA7.Signal=S_TIM3_CH2
PA8.Signal=I2C3_SCL
PB0.GPIO_Label=RF3_G
PB0.Signal=GPIO_Input
PB1.GPIO_Label=LED_DBG1
PB1.Signal=GPIO_Output
PB10.Signal=I2C2_SCL
PB13.GPIO_Label=M3_4
PB13.Signal=GPIO_Output
PB14.GPIO_Label=SERVO1
PB14.Signal=S_TIM12_CH1
PB15.GPIO_Label=SERVO2
PB15.Signal=S_TIM12_CH2
PB2.GPIO_Label=M1_2
PB2.Signal=GPIO_Output
PB3.GPIO_Label=SWO
PB3.Signal=SYS_JTDO-SWO
PB4.Signal=I2C3_SDA
PB5.GPIO_Label=M2_4
PB5.Signal=GPIO_Output
PB6.GPIO_Label=M1_1
PB6.Signal=S_TIM4_CH1
PB7.GPIO_Label=M1_3
PB7.Signal=S_TIM4_CH2
PB8.GPIO_Label=M2_1
PB8.Signal=S_TIM4_CH3
PB9.GPIO_Label=M2_3
PB9.Signal=S_TIM4_CH4
PC0.GPIO_Label=RF1_G
PC0.Signal=GPXTI0
PC1.GPIO_Label=RF2_G
PC1.Signal=GPXTI1
PC10.GPIO_Label=LED_DBG2
PC10.Signal=GPIO_Output
PC11.GPIO_Label=RF6_G
PC11.Signal=GPIO_Input
PC12.Signal=I2C2_SDA
PC13.GPIO_Label=B1 [Blue PushButton]
PC13.Signal=GPXTI13
PC14-OSC32_IN.Signal=RCC_OSC32_IN
PC15-OSC32_OUT.Signal=RCC_OSC32_OUT
PC2.GPIO_Label=SW1
PC2.Signal=GPIO_Output
PC3.GPIO_Label=SW3
PC3.Signal=GPIO_Output
PC4.GPIO_Label=M3_2
PC4.Signal=GPIO_Output
PC5.GPIO_Label=SW2
PC5.Signal=GPIO_Output
PC6.GPIO_Label=SW4
PC6.Signal=GPIO_Output
PC7.GPIO_Label=M1_4
PC7.Signal=GPIO_Output
PH0-OSC_IN.Signal=RCC_OSC_IN
PH1-OSC_OUT.Signal=RCC_OSC_OUT

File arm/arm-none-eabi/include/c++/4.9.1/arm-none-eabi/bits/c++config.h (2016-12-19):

// Predefined symbols and macros -*- C++ -*-

// Copyright (C) 1997-2014 Free Software Foundation, Inc.
//
// This file is part of the GNU ISO C++ Library.  This library is free
// software; you can redistribute it and/or modify it under the
// terms of the GNU General Public License as published by the
// Free Software Foundation; either version 3, or (at your option)
// any later version.

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
// Under Section 7 of GPL version 3, you are granted additional
// permissions described in the GCC Runtime Library Exception, version
// 3.1, as published by the Free Software Foundation.

// You should have received a copy of the GNU General Public License and
// a copy of the GCC Runtime Library Exception along with this program;
// see the files COPYING3 and COPYING.RUNTIME respectively.  If not, see
// <http://www.gnu.org/licenses/>.

/** @file bits/c++config.h
 *  This is an internal header file, included by other library headers.
 *  Do not attempt to use it directly. @headername{iosfwd}
 */

#ifndef _GLIBCXX_CXX_CONFIG_H
#define _GLIBCXX_CXX_CONFIG_H 1

// The current version of the C++ library in compressed ISO date format.
#define __GLIBCXX__ 20140716

// Macros for various attributes.
//   _GLIBCXX_PURE
//   _GLIBCXX_CONST
//   _GLIBCXX_NORETURN
//   _GLIBCXX_NOTHROW
//   _GLIBCXX_VISIBILITY
#ifndef _GLIBCXX_PURE
# define _GLIBCXX_PURE __attribute__ ((__pure__))
#endif

#ifndef _GLIBCXX_CONST
# define _GLIBCXX_CONST __attribute__ ((__const__))
#endif

#ifndef _GLIBCXX_NORETURN
# define _GLIBCXX_NORETURN __attribute__ ((__noreturn__))
#endif

// See below for C++
#ifndef _GLIBCXX_NOTHROW
# ifndef __cplusplus
#  define _GLIBCXX_NOTHROW __attribute__((__nothrow__))
# endif
#endif

// Macros for visibility attributes.
//   _GLIBCXX_HAVE_ATTRIBUTE_VISIBILITY
//   _GLIBCXX_VISIBILITY
# define _GLIBCXX_HAVE_ATTRIBUTE_VISIBILITY 1

#if _GLIBCXX_HAVE_ATTRIBUTE_VISIBILITY
# define _GLIBCXX_VISIBILITY(V) __attribute__ ((__visibility__ (#V)))
#else
// If this is not supplied by the OS-specific or CPU-specific
// headers included below, it will be defined to an empty default.
# define _GLIBCXX_VISIBILITY(V) _GLIBCXX_PSEUDO_VISIBILITY(V)
#endif

// Macros for deprecated attributes.
//   _GLIBCXX_USE_DEPRECATED
//   _GLIBCXX_DEPRECATED
#ifndef _GLIBCXX_USE_DEPRECATED
# define _GLIBCXX_USE_DEPRECATED 1
#endif

#if defined(__DEPRECATED) && (__cplusplus >= 201103L)
# define _GLIBCXX_DEPRECATED __attribute__ ((__deprecated__))
#else
# define _GLIBCXX_DEPRECATED
#endif

// Macros for ABI tag attributes.
#ifndef _GLIBCXX_ABI_TAG_CXX11
# define _GLIBCXX_ABI_TAG_CXX11 __attribute ((__abi_tag__ ("cxx11")))
#endif


#if __cplusplus

// Macro for constexpr, to support in mixed 03/0x mode.
#ifndef _GLIBCXX_CONSTEXPR
# if __cplusplus >= 201103L
#  define _GLIBCXX_CONSTEXPR constexpr
#  define _GLIBCXX_USE_CONSTEXPR constexpr
# else
#  define _GLIBCXX_CONSTEXPR
#  define _GLIBCXX_USE_CONSTEXPR const
# endif
#endif

// Macro for noexcept, to support in mixed 03/0x mode.
#ifndef _GLIBCXX_NOEXCEPT
# if __cplusplus >= 201103L
#  define _GLIBCXX_NOEXCEPT noexcept
#  define _GLIBCXX_USE_NOEXCEPT noexcept
#  define _GLIBCXX_THROW(_EXC)
# else
#  define _GLIBCXX_NOEXCEPT
#  define _GLIBCXX_USE_NOEXCEPT throw()
#  define _GLIBCXX_THROW(_EXC) throw(_EXC)
# endif
#endif

#ifndef _GLIBCXX_NOTHROW
# define _GLIBCXX_NOTHROW _GLIBCXX_USE_NOEXCEPT
#endif

#ifndef _GLIBCXX_THROW_OR_ABORT
# if __EXCEPTIONS
#  define _GLIBCXX_THROW_OR_ABORT(_EXC) (throw (_EXC))
# else
#  define _GLIBCXX_THROW_OR_ABORT(_EXC) (__builtin_abort())
# endif
#endif

// Macro for extern template, ie controling template linkage via use
// of extern keyword on template declaration. As documented in the g++
// manual, it inhibits all implicit instantiations and is used
// throughout the library to avoid multiple weak definitions for
// required types that are already explicitly instantiated in the
// library binary. This substantially reduces the binary size of
// resulting executables.
// Special case: _GLIBCXX_EXTERN_TEMPLATE == -1 disallows extern
// templates only in basic_string, thus activating its debug-mode
// checks even at -O0.
# define _GLIBCXX_EXTERN_TEMPLATE 1
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

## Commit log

2016-12-09 Compiled newlib for stm32f4. Replaced libc.a, libm.a
2016-12-09 Added solidworks
    [0.125_pulley.SLDPRT, 0.25_pulley.SLDPRT, Kornylak Transwheel.SLDASM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]
2016-12-09 Added stuff
    [6383K213_BALL BEARING.SLDPRT, TheRealOmniWheel.SLDPRT, base_board.SLDPRT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]
2016-12-09 Fixed commit sync between mac and w10
    [i2c.c, main.c, main.h]
2016-12-09 Added HAL libs, replaced main.c main.h, replaced system files, working on startup file.
    [main.c]
2016-12-09 Updated the system files and replaced main again.
    [main.c, main.h]
2016-12-19 Fixing commits...
    [st_nucleo_f4.cfg]
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2017-01-10 Regenerated cube code with correct clock config
    [main.c]
2017-01-10 Modified some files. Not working yet
    [main.c, main.h]
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2017-01-30 Changed I2C stuff. DMA fifo to normal mode. Replaced some hardcoded stuff with defines in config file.
    [i2c.c, main.c]
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2017-02-01 I2C write works. Read is missing stop bit
    [i2c.c, main.c]
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2017-09-24 Added datasheets, enabled leaky integrator
    [main.c]
2017-09-25 Fixed a pinout problem with C15. Sensor reading fixed
    [main.c, main.h]
2017-10-04 Added Gantt chart
    [gantt.xlsx]
2017-10-04 Updated page layout and added gantt.pdf
    [gantt.xlsx]
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2017-11-05 PWM working! Fixed motor gpio pinout
    [main.c, main.h, tim.h]
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2017-11-06 Fixed magnetometer calcs. Added basic proportional angle control experiment
    [rangeRead.py]
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2017-11-07 Fixed a bug where the magnetometer would stop working.
    [i2c.c]
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2017-11-07 Added thread locking to prevent some threading errors
    [rangeRead.py]
2017-11-07 Fixed another threading error when closing
    [rangeRead.py, robot.py]
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2017-11-13 Added I2C_Scan function. Fixed gyro issue. Actually a different part than expected.
    [i2c.c, imu.c, main.c]
2017-11-13 Improved data output jitter
    [main.c]
2017-11-13 Communication to imu gui working now. Some errors with missing characters though
    [cal_gui.py, main.c, usart.c]
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2017-11-16 Updated documentation, added calibration routines
    [rangefinder_data.xlsx]
2017-11-16 Swapped variables to use RunningStat class
    [helper_funcs.py, robot.py, robot_gui.py]
2017-11-16 Enabled HPF on IMU accel. Swapped kalman for unscented
    [imu.c, robot.py, robot_gui.py]
2018-01-04 Added mecanum control with joystick. Added coupler design
    [mecanum_coupler.SLDPRT]
2018-01-11 Added new eagle folder
    [control_board.brd, control_board.sch]
2018-01-11 Added battery and regulators. Added silks to nucleo footprint.
    [control_board.brd, control_board.sch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]
2018-01-17 Added connectors, more layout stuff
    [control_board.brd, control_board.sch]
2018-01-17 Added more stuff
    [control_board.brd, control_board.sch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]
2018-01-18 Added cube, gpio expander, rearranged gpios
    [control_board.brd, control_board.sch]
2018-01-18 Nearly done assigning gpio
    [control_board.brd, control_board.sch]
2018-01-18 Finished mapping GPIOs. Need to cross check.
    [control_board.brd, control_board.sch]
2018-01-18 Added clock config to cube
    [control_board.sch]
2018-01-18 Added configs in Cube.
    [control_board.brd, control_board.sch]
2018-01-25 Almost done routing
    [control_board.brd, control_board.sch]
2018-01-25 Routing complete. Need GND stitching
    [control_board.brd, control_board.sch]
2018-01-25 GND stitching done
    [control_board.brd]
2018-01-25 Layout done!
    [control_board.brd]
2018-01-25 PCB complete
    [control_board.brd, control_board.sch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]
2018-01-31 Added electrical mounting
    [Kornylak Transwheel.SLDASM, NUCLEO_F446RE.SLDPRT, NUCLEO_F446RE_assem.SLDASM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]
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2018-02-03 Almost done with flywheel cage
    [cage.SLDPRT, flywheel_cage.SLDASM, flywheel_cage.SLDPRT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]
2018-02-03 Completed rev 1 of flywheel cage
    [bearing.SLDPRT, cage.SLDPRT, cage.STL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]
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2018-02-05 Added blower, modified cage to have more crush, adding venturi feeder
    [blower.SLDPRT, cage.SLDPRT, cage_test_bulge.SLDPRT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]
2018-02-07 Started new dual flywheel cage
    [blower.SLDPRT, cage.SLDPRT, dual_flywheel_cage.SLDASM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]
2018-02-07 Need to add connection to blower on venturi_loader
    [cage.SLDPRT, cage.STL, cage_test_bulge.SLDPRT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]
2018-02-08 Finished dual wheel launcher but need to add mounting points to the rest of robot and to hopper
    [2.3mm_hole_test.SLDPRT, 2.3mm_hole_test.STL, blower.SLDPRT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]
2018-02-08 Finished adding mount points to launcher. Need to add hopper feed mount
    [dual_flywheel_cage.SLDASM, dual_flywheel_cage.SLDPRT, launcher.SLDASM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]
2018-02-08 Dual wheel launcher v1 complete.
    [dual_flywheel_cage.SLDPRT, dual_flywheel_cage.STL, launcher.SLDASM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]
2018-02-09 Finished straight feeder tube
    [0.125_pulley.SLDPRT, 0.25_pulley.SLDPRT, 6383K213_BALL BEARING.SLDPRT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]
2018-02-11 Finalized venturi loader. Added rangefinder and mount
    [dual_flywheel_cage.SLDASM, electrical_mount.SLDPRT, electrical_mount_assem.SLDASM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]
2018-02-11 Started electrical mounting bracket
    [battery.SLDPRT, electrical_mount.SLDPRT, electrical_mount_assem.SLDASM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]
2018-02-11 Revised electrical mounting and chassis
    [NUCLEO_F446RE.SLDPRT, blower.SLDPRT, bottom_plate.SLDPRT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]
2018-02-12 New mounting solution for electrical board
    [bottom_plate.SLDPRT, buck_converter.SLDPRT, buck_converter_standoff.SLDASM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]
2018-02-12 Added extra holes to bottom plate
    [bottom_plate.SLDPRT]
2018-02-13 Added missing assems
    [robot_assem.SLDASM, robot_base.SLDASM]
2018-02-15 Added hopper and field with supply tube
    [bottom_plate.SLDPRT, electrical_mount_bracket_small.STL, field_supply_side.SLDASM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]
2018-02-16 Added new hopper with servo
    [field_supply_side.SLDASM, hopper.SLDASM, robot_assem.SLDASM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]
2018-02-16 Added mounting for motor drivers, hopper base fix for motor mount screws, added missing screw hole for launcher mount and fixed spacing
    [battery.SLDPRT, bottom_plate.SLDPRT, drive_motor_assem.SLDASM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]
2018-02-16 Added drawings for laser
    [hopper.SLDASM, robot_assem.SLDASM, servo_hopper.SLDPRT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]
2018-02-16 Fixed hopper alignment
    [hopper.SLDASM, robot_assem.SLDASM, servo_hopper.SLDPRT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]
2018-02-16 Added fillets to mount base
    [electrical_mount_bracket_angled.STL, servo_hopper_mount_base.SLDPRT, servo_hopper_mount_base.STL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]
2018-02-22 Added new firmware from cube. Added servo and imu mount
    [hopper.SLDASM, hopper_servo_mount.SLDASM, m2-8.SLDPRT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]
2018-02-22 Make works on new firmware
    [st_nucleo_f4.cfg]
2018-02-22 Fixed usart DMA, improved console python script
    [console.py, i2c.c, imu.c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]
2018-02-23 Changed .ioc to switch sw1-4 to outputs
    [control_board.sch]
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2018-02-24 Added missing interrupts in cube
    [firmware_new.ioc, i2c.c, main.c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]
2018-02-24 Fixed USART TX DMA. Works great!
    [i2c.c, main.c, usart.c]
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2018-03-01 Frame skipping added
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2018-03-01 Added IMU and noise to measurements
    [simulator.py]
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2018-03-30 Fixed bug in model restore code
    [ddpg.py]
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2018-04-05 Created switch and battery mount. Improved robotsim but currently not working. Need to add actualXY sensor
    [battery.SLDPRT, battery_mount.SLDPRT, battery_mounted.SLDASM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]
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2018-04-06 Added shutdown script. Improved tranx training
    [battery_mount.SLDPRT, battery_mounted.SLDASM, button.SLDPRT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]
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2018-04-09 Fixing magnetometer issues
2018-04-10 Fixed mcu watchdog, fixed mecanum motor numbering.
    [console.py, main.c, main.h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]
2018-04-10 Added leaky integrator filters to imu data
    [imu.c, main.c, pi_client.py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]
2018-04-11 Fixed IMU accel/mag read errors. Accel needed right-shift by 4. Mag data HI/LO registers were backwards
    [cal_gui.py, imu.c, robot.py]
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2018-04-11 Angle network working but still needs tuning. Keeps overshooting
    [console.py, main.c, pi_client.py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]
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2018-04-13 State machine done. Needs to be tested. Likely full of bugs
    [robot.py]
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2018-05-05 Tilt compass not working properly... Fixing
    [imu.c, main.c, pi_client.py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]
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2018-05-11 Added more fasteners to models. Split robot assembly into the primary subassemblies. Rendered some parts. Fixed figure sizing and placement. Added more info to mechanical chapter
    [base_platform.SLDASM, battery.SLDPRT, battery_mount.SLDPRT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]
2018-05-14 Added more images to mechanical chapter, more work on electrical chapter
    [base_platform.SLDASM, dual_flywheel_cage_fixed.SLDASM, electrical_mount_assem.SLDASM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]
2018-05-16 Removed some old files. Updated electrical chapter with more sensor info
    [0.125_pulley.SLDPRT, 0.25_pulley.SLDPRT, 6383K213_BALL BEARING.SLDPRT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]
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2018-05-25 Added more fasteners to model. Added mech bom. Added render of motor assembly exploded. Fixed pcb bom. Added more to mech chapter
    [BOM.xls, base_platform.SLDASM, drive_motor_assem.SLDASM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]
2018-05-25 Added button, updated BOM, fixed some typos in mechanical chapter, redid top, front, iso renders
    [BOM.xls, base_platform.SLDASM, button_mounted.SLDASM]
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2018-05-27 Fixed some plot problems. Starting neural chapter
    [ann_plot.py, ddpg.py]
2018-05-27 Fixed some code to get transx and trany training working
    [ann_plot.py, ddpg.py, robot.py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]
2018-05-28 Improved multipage table format. Fixed some training reset errors
    [ddpg.py, robot.py, robotsim.py]
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2018-06-03 Added more to results. Fixed scientific notation issue in intro
    [training progress.xlsx]
2018-06-06 Fixed some bib refs. Fixed network diagrams. Improved reward code.
    [ann.py, ddpg.py, robotsim.py]
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2018-06-07 Added gif to presentation, redid flowchart
    [training progress.xlsx]
2018-06-07 Redid all result figures
    [training progress.xlsx]
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2018-06-08 Finished slides. Need to finish 3 actor sim.
    [training progress.xlsx]
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

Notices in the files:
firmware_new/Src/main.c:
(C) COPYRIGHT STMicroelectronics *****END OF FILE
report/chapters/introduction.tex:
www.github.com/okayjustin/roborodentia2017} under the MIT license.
